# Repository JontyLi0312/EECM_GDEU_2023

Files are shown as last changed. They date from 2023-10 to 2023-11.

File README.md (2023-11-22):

# 2023 广东省大学生工科实验综合大赛\_全地形越障运送小车

MCU: STM32F407ZGT6

Keil project，base on AC6

## Category

1. Module
2. Pins
3. Code Description
4. Usage
5. Contributor
6. Contact
7. History

## Module

1. DC gear motor (JGB-520) with encoder
2. servo
3. jy901s
4. MP1584EN
5. OLED
6. 5 channel gray scale sensor

## Pins

### OpenMV

**UART5**

TX -> PC12

RX -> PD2

### DC gear motor 1

**TIM1**

encoder A -> PA8

encoder B -> PE11

**TIM3_CH1**

PWM -> PB4

**GPIO**

IN1 -> PC0

IN2 -> PC1

### DC gerat motor 2

**TIM8**

encoder A -> PC6

encoder B -> PC7

**TIM3_CH2**

PWM -> PA7

**GPIO**

IN1 -> PC2

IN2 -> PC3

### DC gerat motor 3

**TIM2**

encoder A -> PA15

encoder B -> PB3

**TIM3_CH3**

PWM -> PC8

**GPIO**

IN1 -> PC4

IN2 -> PC5

### DC gerat motor 4

**TIM4**

encoder A -> PB6

encoder B -> PB7

**TIM3_CH4**

PWM -> PC9

**GPIO**

IN1 -> PC10

IN2 -> PC11

### Servo

**TIM5**

top servo PWM -> PA2

buttom servo PWM -> PA1

### OLED

**IIC**

SCL -> PG12

SDA -> PG11

### jy901s

**USART2**

RX -> PA3

TX -> PD5

### 5 channel gray scale sensor

**GPIO**

left -> PB11

mid_left -> PB12

mid -> PB13

mid_right -> PE13

right -> PB15

### stop button

**GPIO**

stop -> PG14

## Code Description

### Hardware

- OLED

  - OLED 显示
- 5ChannelGrayScaleSensor

  - 五路灰度扫描循迹并返回方向
- jy901s

  - 获取小车姿态
  - 私有通信协议
- motor

  - 编码器初始化
  - 电机控制
  - PID 算法
- OPENMV

  - 颜色识别
- servo

  - 舵机 PWM
  - 舵机控制

### System

- Delay

  - 延时
- motor_PWM

  - 电机 PWM
- sys

  - 头文件
- Timer

  - 定时中断初始化
- uart5

  - 串口 5 初始化
- usart

  - 串口 1 初始化
  - printf 函数重定义
- usart2

  - 串口 2 初始化

### User

- main
  - 主程序

## Usage

1. 通电
2. 按下 reset 按钮
3. 越过障碍
4. OPENMV 识别色卡
5. 匹配色卡
6. 倾倒弹珠

## Contributor

Jonty Li, Tender Zephyr, coolersf

## History

version 0.1.0: initialize

version 0.2.0：增加开始按钮与颜色选择按钮

version 0.3.0：增加 LED 显示颜色选择结果

version 0.4.0：移除 LED 显示颜色选择结果

version 0.5.0：增加对直流减速编码电机的支持

version 0.6.0：增加舵机控制

version 0.7.0：增加 jy901s 获取角度信息

version 0.8.0：增加五路灰度传感器获取方向信息

version 0.9.0：电机 PID

version 0.10.0：OPENMV 颜色识别

version 0.11.0：根据小车姿态数据调整速度

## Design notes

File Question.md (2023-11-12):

# Project Question

1. 过早画PCB
2. 没有保护main branch
3. 创建branch前应先sync云仓库最新版本
4. 提交逻辑混乱
5.

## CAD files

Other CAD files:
docs/schematic/亚克力底板图纸/亚克力底板.dwg

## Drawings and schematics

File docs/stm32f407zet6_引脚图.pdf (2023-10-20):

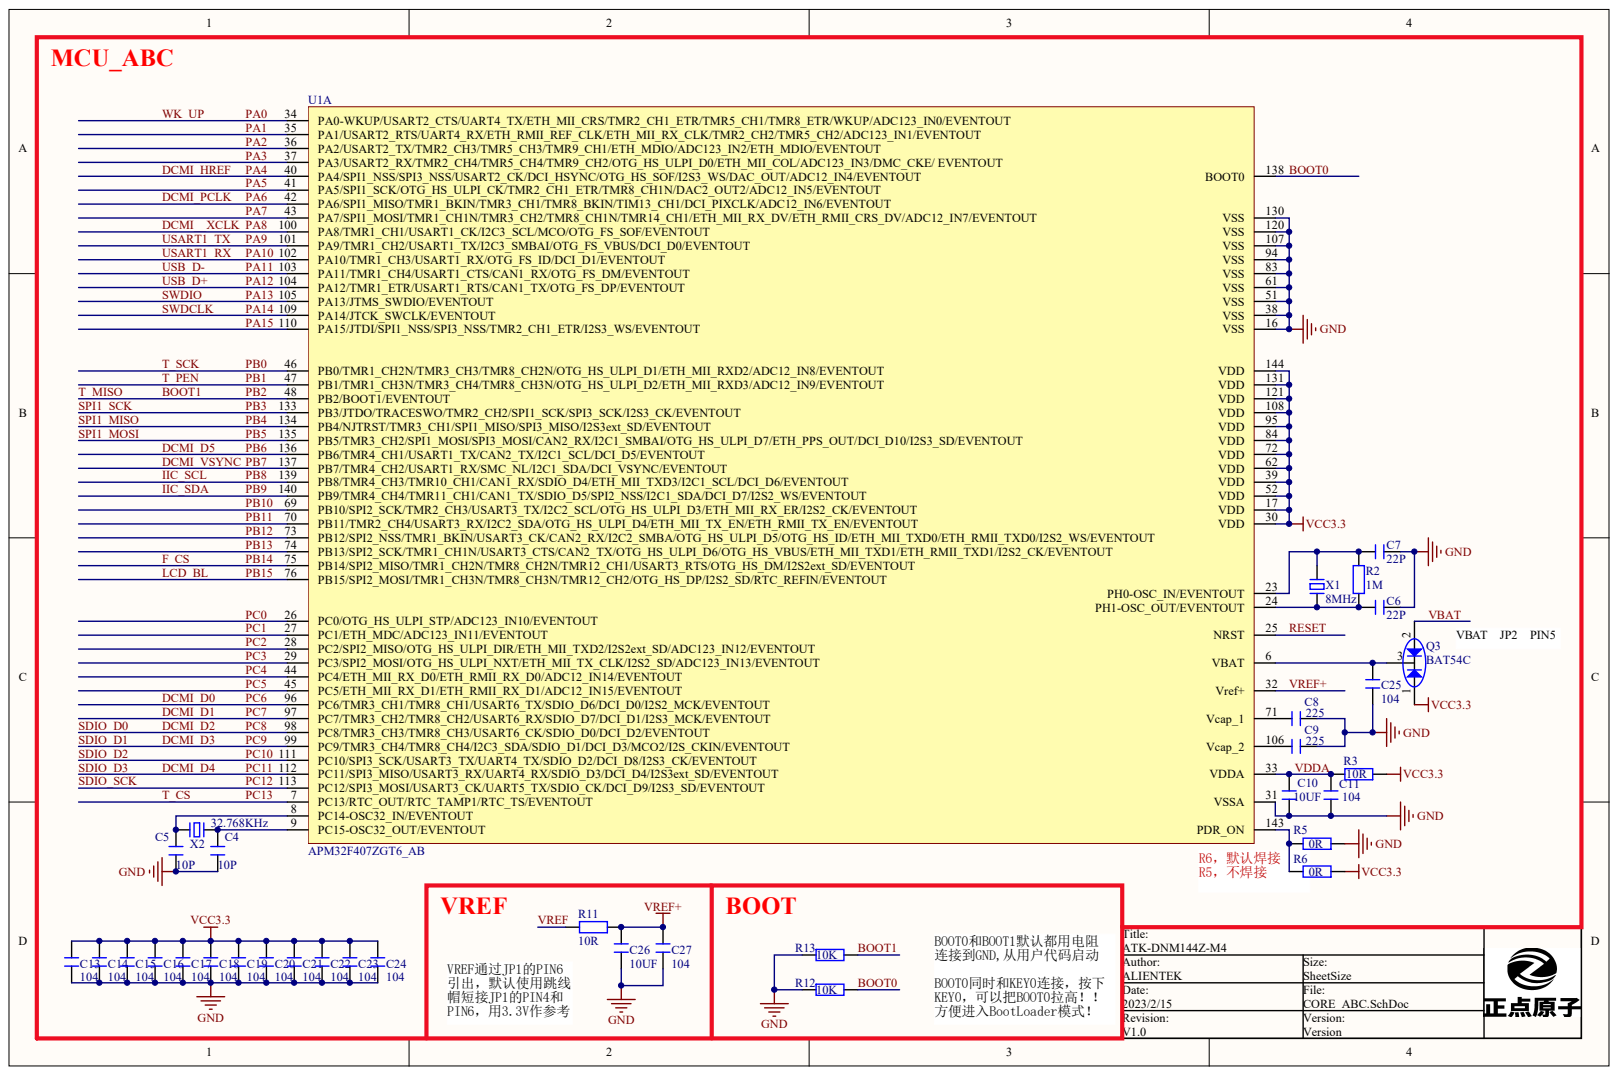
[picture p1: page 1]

1 | 2 0
1 | 0 7

1 | 3 1
1 | 2 1
1 | 0 8

2 4

VREF +

Title: Author: ATK-DNM14 4Z-M 4

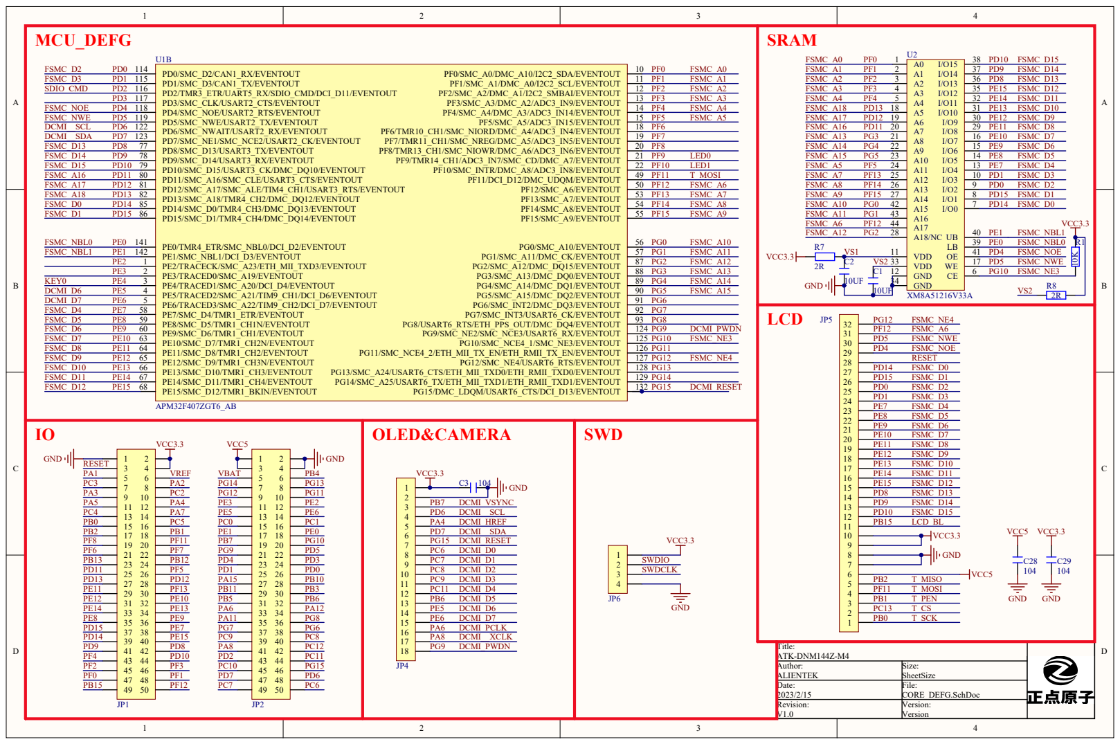
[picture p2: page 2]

V S 2 3 3 | | 1 7 F S MC_NW E
1 2 | | 6 PG1 0 F S MC_NE3

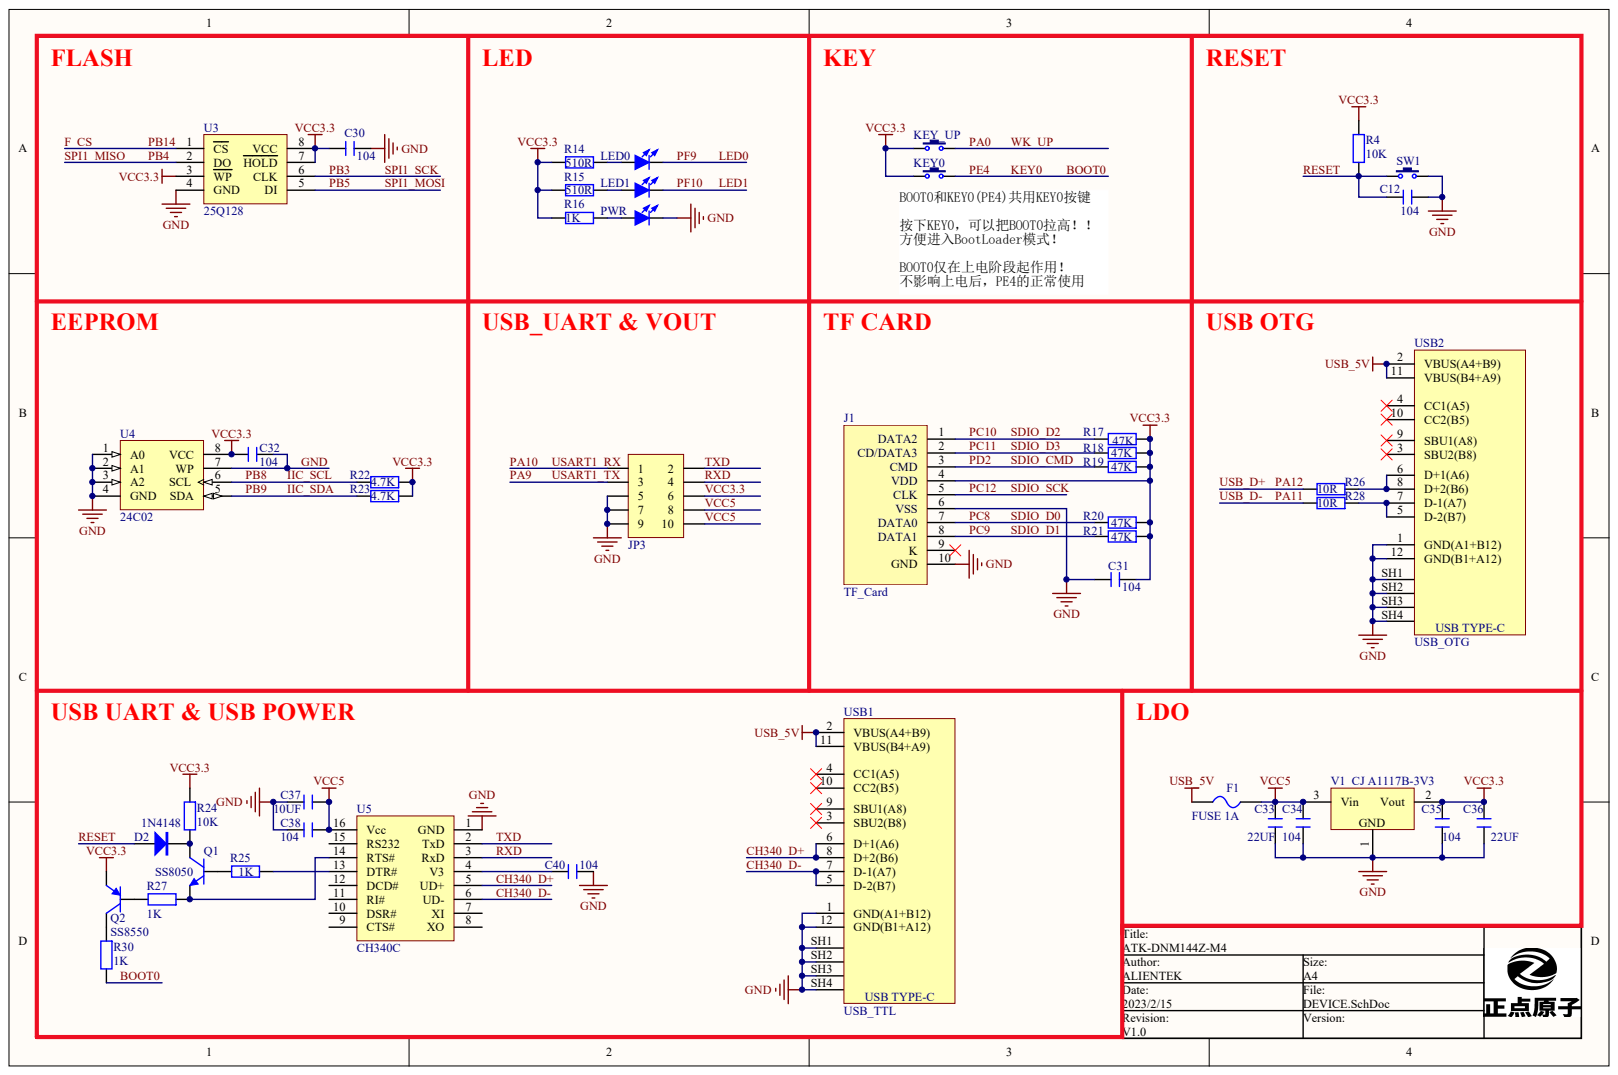
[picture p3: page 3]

Shield1 SH1
Shield2 SH2
Shield3 SH3
Shield4 SH4

GND(B1+A12) 12

Author: ALIENTEK | Size: A4

Date: 2023/2/15 | File: DEVICE.SchDoc

Revision: V1.0 | Version:

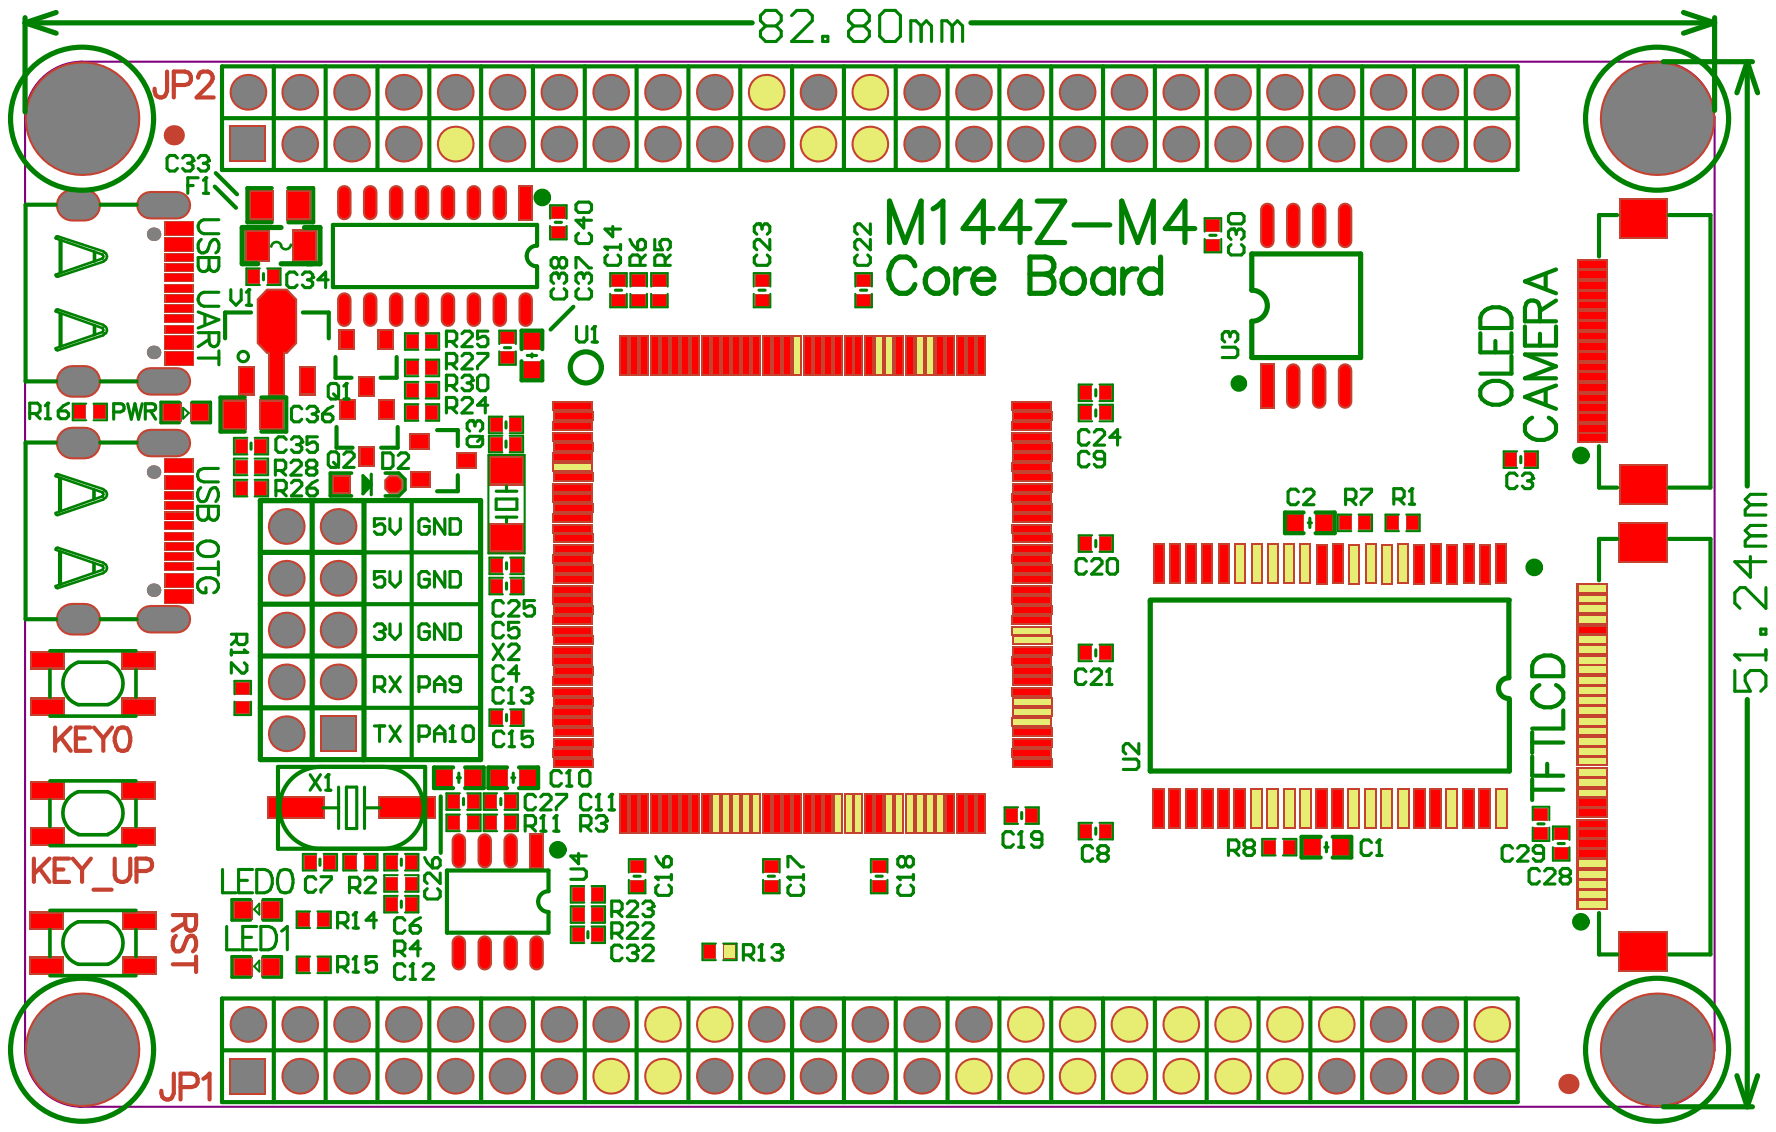
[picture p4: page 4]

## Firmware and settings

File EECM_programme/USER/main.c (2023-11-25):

/**
 * @file main.c
 * @author Jonty (ljt20030312@Outlook.com)
 * @date 2023-10-08
 * @brief EECM_main.c
 */

#include <stdio.h>
#include <string.h>
#include "sys.h"
#include "delay.h"
#include "oled.h"
#include "motor.h"
#include "jy901s.h"
#include "5graysacle.h"
#include "Timer.h"
#include "encoder_PID.h"
#include "UART5.h"
#include "servo_apply.h"
#include "drive.h"
#include "motor_encoder.h"
#include "servo_control.h"

u8 g_Serial_RxPacket[5] = { '0', '0', '0', '0', '0' };
u8 g_servo_start = 0;
int g_jy901s_stop = 0;
/**
 * @brief 小车绝对姿态数据
 *
 */
jy901s_angleData g_angleDatas;

int main(void)
{
    struct datas {
        /**
         * @brief 小车基准姿态数据
         *
         */
        float base_roll;
        float base_pitch;
        float base_yaw;

        /**
         * @brief 小车在(min, max)内则认为小车水平
         *
         */
        float horizontal_pitch_max;
        float horizontal_pitch_min;
        /**
         * @brief 小车角度>up_pitch则认为在爬升，小车角度<down_pitch则认为在向下
         *
         */
        float up_pitch;
        float down_pitch;

        /**
         * @brief 正常速度以及下阶梯速度
         *
         */
        int16_t normal_speed;
        int16_t low_speed;
    }baseDatas;
    baseDatas.normal_speed = 30;
    baseDatas.low_speed = 13;
    baseDatas.up_pitch = 10.00;
    baseDatas.down_pitch = -10.00;
    baseDatas.horizontal_pitch_max = 4.00;
    baseDatas.horizontal_pitch_min = -4.00;

    struct flag
    {
        /**
        * @brief 爬坡标志位,下坡标志位
        *
        */
        u8 upslope;
        u8 downhill;

        /**
        * @brief 暂停再启动标志位,低速行驶标志位
        *
        */
        u8 lowSpeed;
        u8 restart;

        /**
         * @brief 爬坡标志位
         *
         */
        u8 climb_stop;
    }flag;
    flag.downhill = 0;
    flag.upslope = 0;
    flag.lowSpeed = 0;
    flag.restart = 0;
    flag.climb_stop = 0;

    u8 direction;
    jy901s_angleData angle_correction;

    NVIC_PriorityGroupConfig(NVIC_PriorityGroup_2);
    delay_init(168);
    OLED_Init();
    motor_init();
    jy901s_init();
    grayscale_init();
    PID_Init();
    Uart5_init();
    TIM6_Init();
    Servo_Init();
    Servo_Reset();

    OLED_Clear();
    OLED_ShowString(0, 0, (unsigned char*)"Status: WORKING", 8, 1);

    /**
     * @brief 获取小车基准姿态
     *
     */
    jy901s_getData(&g_angleDatas);
    baseDatas.base_pitch = g_angleDatas.pitch;
    baseDatas.base_roll = g_angleDatas.roll;
    baseDatas.base_yaw = g_angleDatas.yaw;

    while (1)
    {
        /**
         * @brief 得到小车相对值姿态数据
         *
         */
        angle_correction.pitch = g_angleDatas.pitch - baseDatas.base_pitch;

        if (angle_correction.pitch >= baseDatas.up_pitch)
        {
            flag.upslope++;
        }
        else if (angle_correction.pitch <= baseDatas.down_pitch)
        {
            flag.downhill++;
        }
        else if ((angle_correction.pitch < baseDatas.horizontal_pitch_max) &&
            (angle_correction.pitch > baseDatas.horizontal_pitch_min))
        {
            if ((flag.upslope != 0) || (flag.downhill != 0))
            {
                if (flag.upslope)
                {
                    flag.restart++;
                }
                else if (flag.downhill)
                {
                    flag.lowSpeed++;
                }
                flag.upslope = 0;
                flag.downhill = 0;
            }
        }

        if (flag.lowSpeed == 3)
        {
            flag.lowSpeed = 0;
            flag.restart = 0;
        }

        OLED_ShowNum(0, 40, flag.restart, 1, 8, 1);
        OLED_ShowNum(20, 40, flag.lowSpeed, 1, 8, 1);

        if (g_servo_start == 1)
        {
            g_jy901s_stop = 1;
            stop();
            Servo_Action();
            delay_ms(1500);
            Servo_Reset();
            delay_ms(1000);
            g_servo_start = 2;
            g_jy901s_stop = 0;

        }
        else if (g_servo_start == 2)
        {
            Servo_Init();
            delay_ms(3000);
        }

        direction = grayScale_detect();
        if (direction == 'l')
        {
            // turn left
            OLED_ShowString(0, 20, (unsigned char*)" <- ", 8, 1);

            turn_left(30, 0);
        }
        else if (direction == 'r')
        {
            // turn right
            OLED_ShowString(0, 20, (unsigned char*)" -> ", 8, 1);

            turn_right(30, 0);
        }
        else if (direction == 'L')
        {
            // turn left
            OLED_ShowString(0, 20, (unsigned char*)"<<--", 8, 1);

            turn_left(45, 10);
        }
        else if (direction == 'R')
        {
            // turn right
            OLED_ShowString(0, 20, (unsigned char*)"-->>", 8, 1);

            turn_right(45, 10);
        }
        else
        {
            OLED_ShowString(0, 20, (unsigned char*)" GO ", 8, 1);

            if ((flag.lowSpeed > 0) && (flag.lowSpeed < 3) && (flag.restart == 3))
            {
                if (flag.climb_stop > 1)
                {
                    stop();
                    delay_ms(2000);
                    flag.climb_stop = 0;
                }
                stop();
                delay_ms(60);
                forward(baseDatas.low_speed, baseDatas.low_speed);
                delay_ms(30);
            }
            else if (flag.restart == 2)
            {
                if (!flag.climb_stop)
                {
                    stop();
                    delay_ms(1000);
                    flag.climb_stop++;
                }

                forward(baseDatas.normal_speed, baseDatas.normal_speed + 8);
                flag.climb_stop++;
            }
            else if ((flag.lowSpeed == 1) && (flag.upslope > 0))
            {
                forward(baseDatas.normal_speed, baseDatas.normal_speed + 10);
            }
            else if ((flag.restart == 0) && (flag.lowSpeed == 0))
            {
                forward(baseDatas.normal_speed + 8, baseDatas.normal_speed + 8);
            }
            else
            {
                forward(baseDatas.normal_speed, baseDatas.normal_speed);
            }
        }
        OLED_Refresh();
    }

    return 0;
}

/**
 * @brief openmv color recognition
 *
 */
void UART5_IRQHandler(void)
{
    static u16 RxState = 0;
    static u16 pRxPacket = 0;
    if (USART_GetITStatus(UART5, USART_IT_RXNE) == SET)
    {
        u8 RxData = USART_ReceiveData(UART5);
        if (RxState == 0)
        {
            if (RxData == '@')
            {
                RxState = 1;
                pRxPacket = 0;
            }
        }
        else if (RxState == 1)
        {
            if (RxData == '%')
            {
                RxState = 2;
            }
            else
            {
                g_Serial_RxPacket[pRxPacket] = RxData;
                pRxPacket++;
            }
        }
        else if (RxState == 2)
        {
            if (RxData == 'A')
            {
                RxState = 0;
                g_Serial_RxPacket[pRxPacket] = '\0';
                
            }
        }
        if (g_Serial_RxPacket[0] == '4')
        {
            g_servo_start = 1;

            
        }
        
        USART_ClearITPendingBit(UART5, USART_IT_RXNE);
    }
}

/**
 * @brief TIM6 interruption: motor PID & servo PID
 *
 */
void TIM6_DAC_IRQHandler(void)
{
    if (TIM_GetITStatus(TIM6, TIM_IT_Update) != RESET) // 在这里执行20ms定时器触发后的操作
    {
        // 让编码器的值变成正整数
        ASR1.Fdb = (Num_Abs(Read_Speed(1)) - 48) / 6.3 + 10;
        ASR2.Fdb = (Num_Abs(Read_Speed(2)) - 48) / 6.3 + 10;
        ASR3.Fdb = (Num_Abs(Read_Speed(3)) - 48) / 6.3 + 10;
        ASR4.Fdb = (Num_Abs(Read_Speed(4)) - 48) / 6.3 + 10;

        ASR1.Err = ASR1.Ref - ASR1.Fdb;
        ASR2.Err = ASR2.Ref - ASR2.Fdb;
        ASR3.Err = ASR3.Ref - ASR3.Fdb;
        ASR4.Err = ASR4.Ref - ASR4.Fdb;

        pid_calc(&ASR1);
        pid_calc(&ASR2);
        pid_calc(&ASR3);
        pid_calc(&ASR4);

        output1 = ASR1.Out;
        output2 = ASR2.Out;
        output3 = ASR3.Out;
        output4 = ASR4.Out;
        PID_apply();
        if (g_jy901s_stop == 0)
        {
            Servo_accomplish();
        }

        jy901s_getData(&g_angleDatas);

        TIM_ClearITPendingBit(TIM6, TIM_IT_Update); // 清除中断标志位
    }
}

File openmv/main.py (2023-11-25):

import sensor, image, time, lcd
from pyb import UART


red_threshold  = (30, 60, 20, 60, -20, 40)
green_threshold  = (30, 66, -50, 0, 0, 61)
blue_threshold  = (35, 60, -16, 33, -60, -10)
sensor.reset()
sensor.set_pixformat(sensor.RGB565)
sensor.set_framesize(sensor.QQVGA)
#sensor.set_windowing((400,400))
sensor.set_auto_gain(True)
sensor.set_auto_whitebal(True)
#sensor.skip_frames(10)
clock = time.clock()
uart = UART(3, 115200) #P4 Tx, P5 Rx--PD2 Rx, PC12 Tx
lcd.init()

flag = '1'
#roi = (40, 40, 80, 80)

def find_max(blobs):
    max_size=0
    for blob in blobs:
        if blob.pixels() > max_size:
            max_blob = blob
            max_size = blob.pixels()
    return max_blob


while(True):
#if uart.any():
    #command = uart.read().decode()
    #if command == 'star':
        while(True):
            img = sensor.snapshot()
            blobs_red = img.find_blobs([red_threshold], roi = (60, 30, 50, 60), pixels_threshold=2800, area_threshold=3000)
            blobs_green = img.find_blobs([green_threshold], roi = (30, 40, 80, 60), pixels_threshold=3500, area_threshold=4000)
            blobs_blue = img.find_blobs([blue_threshold], roi = (40, 30, 80, 60), pixels_threshold=3500, area_threshold=4000)
            if blobs_red:
                max_blob_red=find_max(blobs_red)
                img.draw_rectangle(max_blob_red.rect(), color = (255, 0, 0))
                img.draw_cross(max_blob_red.cx(), max_blob_red.cy())
                lcd.display(img)
                output_str = "red"
                #if max_blob_red.cx() == 64:
                #uart.write("@" + output_str_red + "%" + "A")
                #print(output_str_red)
            elif blobs_green:
                max_blob_green=find_max(blobs_green)
                img.draw_rectangle(max_blob_green.rect(), color = (0, 255, 0))
                img.draw_cross(max_blob_green.cx(), max_blob_green.cy())
                lcd.display(img)
                output_str = "green"
                #if max_blob_green.cx() == 64:
                #uart.write("@" + output_str_green + "%" + "A")
                #print(output_str_green)
            elif blobs_blue:
                max_blob_blue=find_max(blobs_blue)
                img.draw_rectangle(max_blob_blue.rect(), color = (0, 0, 255))
                img.draw_cross(max_blob_blue.cx(), max_blob_blue.cy())
                lcd.display(img)
                output_str = "blue"
                #if max_blob_blue.cx() == 64:
                #uart.write("@" + output_str_blue + "%" + "A")
                #print(output_str_blue)
            else:
                output_str = "none"
                #uart.write("@" + "0" + "%" + "A")
                #print("0")
                lcd.display(img)

            if (flag == '1' and output_str != "none"):
                target = output_str
                flag = '2'
            elif (flag == '2' and output_str == "none"):    #离开目标色块
                flag = '3'
            elif (flag == '3' ):     #寻找匹配色块
                colour = output_str
                if (colour == target):
                    flag = '4'      #找到匹配色块
            elif (flag == '4' and output_str == "none"):
                flag = '5'
                uart.write("@" + '4' + "%" + "A")
                print('4')

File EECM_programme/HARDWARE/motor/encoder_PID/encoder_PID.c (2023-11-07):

#include "encoder_PID.h"
#include "motor_encoder.h"
#include "motor.h"
#include "oled.h"
void PID_Init(void);
void pid_calc(PID *p);
void PID_Move(int16_t speed, int8_t Dre);
void PID_apply(void);
uint16_t Num_Abs(int16_t Encoder);

PID ASR1;
PID ASR2;
PID ASR3;
PID ASR4;
int16_t output1;
int16_t output2;
int16_t output3;
int16_t output4;

/**
 * @brief PID算法初始化
 *
 */
void PID_Init(void)
{
    ASR1.Kp = 6.8;
    ASR1.Ki = 55.81;
    ASR1.Kd = 0.0049;
    ASR1.T = 0.02; //           20ms
    ASR1.OutMax = 90;
    ASR1.OutMin = 0;

    ASR2.Kp = 6.8;
    ASR2.Ki = 55.81;
    ASR2.Kd = 0.0049;
    ASR2.T = 0.02; //           20ms
    ASR2.OutMax = 90;
    ASR2.OutMin = 0;

    ASR3.Kp = 6.8;
    ASR3.Ki = 55.81;
    ASR3.Kd = 0.0049;
    ASR3.T = 0.02; //           20ms
    ASR3.OutMax = 90;
    ASR3.OutMin = 0;

    ASR4.Kp = 6.8;
    ASR4.Ki = 55.81;
    ASR4.Kd = 0.0049;
    ASR4.T = 0.02; //           20ms
    ASR4.OutMax = 90;
    ASR4.OutMin = 0;
}

/**
 * @brief PID算法计算
 *
 * @param p
 */
void pid_calc(PID *p) //
{
    float a0, a1, a2;

    a0 = p->Kp + p->Ki * p->T + p->Kd / p->T;
    a1 = p->Kp + 2 * p->Kd / p->T;
    a2 = p->Kd / p->T;

    p->Out = p->Out_1 + a0 * p->Err - a1 * p->Err_1 + a2 * p->Err_2;

    if (p->Out > p->OutMax) // 限幅
        p->Out = p->OutMax;

    if (p->Out < p->OutMin)
        p->Out = p->OutMin;

    p->Out_1 = p->Out;
    p->Err_2 = p->Err_1;
    p->Err_1 = p->Err;
}

/**
 * @brief PID控速
 *
 * @param speed 速度值（1 - 100）百分比
 * @param Dre 需要控制的电机序号
 */
void PID_Move(int16_t speed, int8_t Dre)
{
    if (Dre == 1) //
    {
        ASR1.Ref = speed / 4.16;
    }
    if (Dre == 2) //
    {

        ASR2.Ref = speed / 4.16;
    }
    if (Dre == 3) //
    {
        ASR3.Ref = speed / 4.16;
    }
    if (Dre == 4) //
    {

        ASR4.Ref = speed / 4.16;
    }
}

/**
 * @brief PWM输入
 *
 */
void PID_apply(void)
{
    int16_t PWM1, PWM2, PWM3, PWM4;

    PWM1 = (int16_t)output1;
    PWM2 = (int16_t)output2;
    PWM3 = (int16_t)output3;
    PWM4 = (int16_t)output4;

    motor1_speed(PWM1);
    motor2_speed(PWM2);
    motor3_speed(PWM3);
    motor4_speed(PWM4);
}

/**
 * @brief 求绝对值
 *
 * @param Encoder 被绝对值的数
 * @return uint16_t
 */
uint16_t Num_Abs(int16_t Encoder)
{
    uint16_t Middle;
    Middle = Encoder > 0 ? Encoder : (-Encoder);
    return Middle;
}

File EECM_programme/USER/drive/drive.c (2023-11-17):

#include "drive.h"
#include "encoder_PID.h"
#include "motor.h"

void turn_left(int16_t f_speed, int16_t b_speed);
void turn_right(int16_t f_speed, int16_t b_speed);
void forward(int16_t font_speed, int16_t back_speed);
void backward(int16_t speed);
void stop(void);

/**
 * @brief 左转程序
 *
 * @param f_speed 前进轮速度
 * @param b_speed 后退轮速度
 */
void turn_left(int16_t f_speed, int16_t b_speed)
{
    motor1_control(1);
    PID_Move(f_speed, 1);
    motor2_control(1);
    PID_Move(f_speed, 2);
    motor3_control(2);
    PID_Move(b_speed, 3);
    motor4_control(2);
    PID_Move(b_speed, 4);
}

/**
 * @brief 右转程序
 *
 * @param f_speed 前进轮速度
 * @param b_speed 后退轮速度
 */
void turn_right(int16_t f_speed, int16_t b_speed)
{
    motor1_control(2);
    PID_Move(b_speed, 1);
    motor2_control(2);
    PID_Move(b_speed, 2);
    motor3_control(1);
    PID_Move(f_speed, 3);
    motor4_control(1);
    PID_Move(f_speed, 4);
}

/**
 * @brief 前进
 *
 * @param speed 前进速度
 */
void forward(int16_t front_speed, int16_t back_speed)
{
    motor1_control(1);
    PID_Move(front_speed, 1);
    motor2_control(1);
    PID_Move(back_speed, 2);
    motor3_control(1);
    PID_Move(back_speed, 3);
    motor4_control(1);
    PID_Move(front_speed, 4);
}

/**
 * @brief 后退速度
 *
 * @param speed
 */
void backward(int16_t speed)
{
    motor1_control(2);
    PID_Move(speed, 1);
    motor2_control(2);
    PID_Move(speed, 2);
    motor3_control(2);
    PID_Move(speed, 3);
    motor4_control(2);
    PID_Move(speed, 4);
}

/**
 * @brief car short brake
 *
 */
void stop(void)
{
    motor1_control(0);
    motor2_control(0);
    motor3_control(0);
    motor4_control(0);
}

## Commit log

2023-09-15 version 0.01 description: create
    [hardware_list.xlsx]
2023-09-15 version 0.02 description: 改动了README.md的目录
2023-09-15 version 0.03 description: 改变了.gitignore文件的目录
2023-09-19 doc(docs): 更改了过往文档的目录，新增了发票
    比赛信息，比赛报名表，hardware.excel更改至新建的docs文件夹下，并且新增invoice文件夹存放发票
    [hardware_list.xlsx]
2023-09-27 doc(README.md, PCB_project): improve documentation
    improve README.md, add PCB_project folder
2023-09-30 description：pcb初步设计
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2023-10-04 ✨ feat(key.c, key.h): 新增按钮功能
    增加了开始按钮，颜色选择按钮
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2023-10-04 🦄 refactor(main.c): 更改了主程序的按键响应逻辑
    初始化完成后等待开始指令，开始后等待选择颜色
2023-10-06 🐞 fix(key.c): 修复无颜色选择时返回值错误
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2023-10-06 ✨ feat(led.c, led.h): 新增了颜色选择对应的led
2023-10-06 🐞 fix(main.c): 修复颜色选择判断语句的语法错误
2023-10-06 🐞 fix(led.c, led.h): 修复分支错误
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2023-10-08 🐞 fix(oled.c): 修复oled无法显示字符串
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2023-10-08 🦄 refactor(main.c, led.c, led.h): 使用oled屏幕显示颜色选择结果，移除led显示结果功能
    使用oled显示颜色选择结果，删除 led.c 和 led.h 文件
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2023-10-08 fix(FWLIB) : 在keil5中移除了stm32f4xx_flash_ramfunc.c文件
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2023-10-08 ✨ feat(motor_PWM.c, motor_PWM.h): 增加减速电机PWM
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2023-10-08 feat(servo_apply.c,servo_apply.h) : 新增调用舵机的相关函数
    增加
    Servo_PWM_Init(void)
    直接调用这个函数初始化
    Servo_SetAngle_Level(floatAngle) Servo_SetAngle_Vertical(float Angle)
    这两个函数是改变舵机的水平和垂直ccr的值
    Servo_Action(void)
    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
2023-10-08 feat(servo_control.c,servo_control.h) : 新增了驱动相关函数
    舵机限幅函数和pid控制舵机以及舵机最后驱动函数
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2023-10-08 ✨ feat(motor): 减速电机初始化，减速电机PWM波初始化
    增加减速电机初始化，增加减速电机PWM波初始化，增加减速电机速度控制，移除main.c中关于led的内容
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2023-10-08 🎉 init(openmv): 增加 openmv目录
2023-10-08 🌈 style(motor.c): 添加代办事项 //todo 减速电机前进后退停止模式控制
2023-10-09 ✨ feat(motor.c, motor.h): 增加减速电机前后转及停止控制
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2023-10-09 ✨ feat(motor.c, motor.h): 完善减速电机速度控制
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2023-10-09 🐞 fix(key.c): 修改开始按钮引脚
    PA3为串口2的引脚，为jy901s的通信引脚
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2023-10-09 fix(README.MD):改变文件的乱码
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2023-10-10 ✨ feat(5graysacle.c, 5graysacle.h): 增加通过五路灰度传感器获取方向函数
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2023-10-11 fix(servo_apply.c):修改调用函数名错误
2023-10-15 refactor(servo_apply.c) : 修改倾倒的角度
    修改的角度使盘子不会碰到云台同时初始的角度放到Servo_PWM_Init()中
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2023-10-20 🐞 fix(main.c): 移除颜色选择功能
2023-10-20 🐞 fix(key.c): 移除颜色选择按钮初始化及按键状态获取
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2023-10-20 🐞 fix(keil project): build project
2023-10-20 🌈 style(5grayscale.c, 5grayscale.h): 修改五路灰度传感器的方向获取
    修改为中间靠左输出低电平时，逻辑右转，中间靠右输出高电平时，逻辑左转，当三者输出高电平时，逻辑前行
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2023-10-21 📃 docs(.gitignore): add ignore file
2023-10-21 📃 docs(*.33281): remove compile file
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2023-10-21 📃 docs(listing): remove target file
2023-10-21 📃 docs(README.md): 修改引脚，新增电路原理图
    [EECM.PrjPcb, Sheet1.SchDoc]
2023-10-22 🐞 fix(motor_PWM.c): 修改电机引脚PC6、PC7至PA6、PA7
2023-10-22 ✨ feat(motor.c, motor_encoder.c, motor_encoder.h): 初始化四个电机编码器模式
    将电机初始化函数将自动调用编码器初始化函数完成初始化
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2023-10-22 fix(servo_PWM.c): 补充舵机的引脚重映射
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2023-10-23 ✨ feat(main.c, key.c, 5grayscale.c): 转弯
    修改五路灰度检测程序方向返回值，修改key.c的代码格式，主函数转弯程序
2023-10-23 🐞 fix(key.c): 更改开始按钮引脚
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2023-10-23 🐞 fix(5grayscale.c): 更改五路灰度传感器引脚
    PB14 -> PE13
    [5grayscale.c]
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2023-10-24 🐞 fix(UART2.c): TX由PA2 -> PD5
    [UART2.c]
2023-10-24 🐞 fix(oled.c, oled.h): SDA由PD5 -> PG11
    [oled.c]
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2023-10-24 🐞 fix(servo_PWM.c, README.c): 云台舵机从TIM4输出PWM改为TIM5
    [servo_PWM.c]
2023-10-24 🐞 fix(motor_encoder.c, README.md): motor4 encoder TIM5 -> TIM4
    PA0, PA1 -> PB6, PB7
    [motor_encoder.c]
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2023-10-24 🐞 fix(motor_encoder.c, servo_PWM.c, UART2.c, README.md): 修改电机编码器，云台，UART2引脚
    [UART2.c, motor_encoder.c, servo_PWM.c]
2023-10-25 📃 docs(README.md): 调整jy901s usart2 tx rx引脚
2023-10-26 🐞 fix(motor.c): 初始化TIM3四个通道，增加亚克力底板cad图纸
    [亚克力底板.dwg]
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2023-10-26 🐞 fix(motor.c, main.c): 更改TIM3_CH1由PA6 -> PB4
    屏蔽按键初始化
    [main.c, motor_PWM.c]
2023-10-26 🐞 fix(motor_encoder.c): TIM1时基结构体增加RepetitionCounter配置
2023-10-26 fix(encoder_PID.c):修改中断函数没加括号的错误
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2023-10-27 📃 docs(亚克力底板.dwg): 完善小车底板cad文件
    [亚克力底板.dwg]
2023-10-27 📃 docs(亚克力底板.dwg): 完善小车亚克力底板
    [亚克力底板.dwg]
2023-10-27 📃 docs(亚克力底板.dwg): 修改亚克力底板cad文件
    [亚克力底板.dwg]
2023-10-27 🐞 fix(motor_encoder.c): 修改TIM1编码器引脚至PE9、PE11
2023-10-27 🐞 fix(motor_PWM.c): 屏蔽PA7输出PWM
2023-10-27 🐞 fix(motor_PWM.c): 取消对TIM3 PWM的屏蔽
    [motor_PWM.c]
2023-10-27 🐞 fix(motor_encoder.c): 更改TIM1 encoder引脚至PA9、PE11
    [motor_encoder.c]
2023-10-27 🐞 fix(main.c): 修改为读取TIM1的编码器的值
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2023-10-27 🐞 fix(motor_PWM.c): 取消屏蔽PA7输出PWM
2023-10-27 🐞 fix(motor_encoder.c): 配置为上拉模式
2023-10-27 🐞 fix(motor_encoder.c): 添加TIM1ARR自动重装
    [亚克力底板.dwg]
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2023-10-27 fix(encoder_PID.c):修改少定义4个output的错误
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2023-10-27 fix(motor.c):修改正反转的代码
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2023-10-28 fix(motor_encoder.c):修改高级定时器挂载总线错误
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2023-10-28 📃 docs(schematic): 新增电路原理图
    [EECM.PrjPcb, Sheet1.SchDoc, parent.SchDoc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]
2023-10-28 📃 docs(schematic\EECM): 完善原理图文件
    [EECM.PrjPcb, MCU.SchDoc, Schlib1.SchLib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]
2023-10-28 📃 docs(.gitignore): 忽略ad preview文件
2023-10-28 📃 docs(schematic): 完成电路原理图
    [Schlib1.SchLib, display.SchDoc, motor.SchDoc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]
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2023-10-28 fix(encoder_PID.c):修改编码器对应函数
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2023-10-29 📃 docs(schematic): 将原理图合为一张
    [MCU.SchDoc, display.SchDoc, motor.SchDoc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]
2023-10-29 fix(motor_encoder.c):修改编码器初始化错误
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2023-10-30 📃 docs(docs): 完成控制系统设计报告
    [MCU.SchDoc, hardware_list.xlsx]
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2023-10-30 🐞 fix(main.c): 移除获取开始按键
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2023-10-30 🧪 test(main.c): test turn_left
2023-10-30 🧪 test(main.c): test turn
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2023-10-30 🧪 test(main.c): test 5 channel gray scale sensor
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2023-10-31 🐞 fix(5grayscale.c): 修复五路灰度方向检测不断返回stop信号的bug
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2023-10-31 🐞 fix(encoder.c): 屏蔽中断进入OLED显示
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2023-10-31 🐞 fix(5grayscale.c): 修改五路灰度判断方向的逻辑
2023-10-31 🐞 fix(5grayscale.c): 修改stop逻辑
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2023-11-01 🐞 fix(5grayscale.c): 修改方向判断逻辑
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2023-11-02 ✨ feat(5grayscale.c): 五路灰度左右传感器消抖
    改变5grayscale.c 的引用逻辑
    主程序消除滤波
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2023-11-04 🧪 test(main.c): remove forward_test_programme
2023-11-04 📃 docs(亚克力底板.dwg): 更新底板孔位
    [亚克力底板.dwg]
2023-11-04 🎉 init(UART5.c and UART5.h): 增加串口5
2023-11-04 ✨ feat(UART5.c, UART5.h): 固定串口5波特率
    baud = 115200
2023-11-04 🐞 fix(UART5.c,UART5.h,main): 删除extern声明
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2023-11-05 📃 docs(亚克力底板.dwg): 取消巡线OPENMV孔位
    复原主控PCB孔位
    [亚克力底板.dwg]
2023-11-06 🐞 fix(key.c & key.h): remove start key file
    BREAKING: remove key file
2023-11-06 🐞 fix(main.c): 转向使用正反转差速转向
2023-11-06 🐞 fix(main.c, motor.c): 调整直行速度，电机停止改为刹车
    [main.c, motor.c]
2023-11-06 🐞 fix(5grayscale.c): 改变转向逻辑
2023-11-06 🐞 fix: 补充转向逻辑
2023-11-06 🧪 test(5grayscale.c): remove "backward"
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2023-11-06 🧪 test(main.c): 改善左右摇摆功能
    停止时左右摇摆结束由检测五路灰度信号非停止信号改为计次
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2023-11-06 🧪 test(main.c): 增大直行速度
    删除stop逻辑
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2023-11-06 ✨ feat(openmv.c and openmv.h): 增加openmv色块识别
2023-11-06 🌈 style(encoder_PID.c, encoder_PID.h): 增加函数注释
2023-11-06 🌈 style(motor.c): 停车的描述改为刹车
    stop - > short brake
    [motor.c]
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2023-11-06 🎈 perf(openmv.c and openmv.h): 删除openmv函数
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2023-11-07 🐞 fix(main.c): 修改小车识别成功不停车
2023-11-07 🐞 fix(main.c): if 嵌套错误
    [main.c]
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2023-11-07 🐞 fix(servo_apply.c): 修改舵机角度
2023-11-07 🐞 fix(servo_apply.c): 继续调整舵机角度
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2023-11-07 🎈 perf(main.c): TIM6 IRQ move to main.c
2023-11-07 🎈 perf(drive): 封装电机行驶控制函数
    function: turn_left, turn_right, forward, backward, stop move to drive.c
    fix openmv bug
    [drive.c, main.c]
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2023-11-07 🐞 fix(main.c): 继续调整舵机角度
2023-11-07 🐞 fix(main.c): 识别完成后多直行500ms
2023-11-07 🐞 fix(main.c): 姿态base value 改为全局变量，增加姿态角的解释注释
    [main.c]
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2023-11-07 🐞 fix(main.c): 完成倒弹珠
2023-11-07 Revert "Merge branch 'feat_20231107_climbStair_speed'"
    This reverts commit 02b98090481d0667e639395a483e06be46da3834, reversing
    changes made to 1176c7609dfe111bd52fca624061dc10bc7b5363.
    [drive.c, encoder_PID.c, main.c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]
2023-11-07 ✨ feat(main.c): get max pitch value
2023-11-07 🐞 fix(.uvprojx): 修复工程文件无法打开
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2023-11-07 🧪 test(main.c): add test comment
2023-11-07 🧪 test(drive.c): add test comment
2023-11-07 🐞 fix(drive.c): 修改文件，用于合并
2023-11-07 🧪 test(drive): remove test comment
2023-11-07 ✨ feat(main.c): show max pitch value
2023-11-07 🐞 fix(main.c): fix merge bug
    [encoder_PID.c, main.c]
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2023-11-08 ✨ feat(main.c): 获取max pitch， 以及爬坡次数
2023-11-08 🧪 test(main.c): openmv test
2023-11-08 🐞 fix(main.c): 中断直接处理识别，执行舵机
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2023-11-08 🐞 fix(main.c): 将舵机执行放到main里面
2023-11-08 ✨ feat(main.c, 5grayscale.c, drive.c, drive.h): 新增大小角度转弯
    转弯函数增加速度形参，增加大小转弯逻辑
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2023-11-09 🐞 fix(5grayscale.c): 调整大小转弯逻辑
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2023-11-09 🐞 fix(5grayscale.c): 修改大小转向逻辑
2023-11-09 🐞 fix(5grayscale.c): 修复大转弯逻辑错误
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2023-11-10 🐞 fix(main.c): 修复无小角度转弯
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2023-11-10 ✨ feat(5grayscale.c): 增加侧边传感器检测黑线大转弯
    当最左边 / 最右边的传感器检测到黑线，其余传感器没有检测到黑线时，为大转弯程序
2023-11-10 🐞 fix(5grayscale.c): 修复大小转弯bug
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2023-11-10 🧪 test(xunxian.py and huiduxunxian.py): openmv巡线test
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2023-11-11 🌈 style(main.c): remove useless comment
2023-11-11 📃 docs(亚克力底板.dwg): 更改孔位，缩短尺寸
    [亚克力底板.dwg]
2023-11-12 📃 docs(Question.md): 增加项目问题文档
    该文档用于记录项目过程中遇到的问题
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2023-11-12 ✨ feat(main.c): 新增小车姿态标志位
    用于判断小车是否需要重启动
2023-11-12 ✨ feat(main.c): 增加小车慢速行驶标志位
    用于小车下阶梯
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2023-11-12 🐞 fix(main.c): 修改慢速行驶逻辑
2023-11-12 📃 docs(亚克力底板.dwg): 更改轴承孔位
    [亚克力底板.dwg]
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2023-11-12 🐞 fix(main.c): 修改舵机启动的全局变量
2023-11-13 🐞 fix(main.c): 修改程序开始时的前进速度
    程序开始时的前进速度与运行时的前进速度保持一致
    [main.c]
2023-11-13 🧪 test(main.c): find horizontal angle
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2023-11-15 🧪 test(main.c): find min speed
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2023-11-17 ✨ feat(drive.c, main.c): 前后轮现可单独控速，新增爬坡时后轮加速
2023-11-17 ✨ feat(main.c): 新增多段速度变化
    降低直行速度
2023-11-17 🌈 style: remove useless spcae line
2023-11-18 📃 docs(亚克力底板.dwg): 更新底板孔位以及发票
    [亚克力底板.dwg]
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2023-11-25 📃 docs(hardware_list.xlsx): 更改硬件清单
    [hardware_list.xlsx]
2023-11-28 📃 docs(docs): 移除含个人信息的文件
    [hardware_list.xlsx]
